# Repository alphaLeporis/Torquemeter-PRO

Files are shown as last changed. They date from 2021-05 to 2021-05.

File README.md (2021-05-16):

# Torquemeter PRO
## Inleiding

Onze koppelmeter is van het type ‘Prony Brake’. Hierbij klemmen we een arm met gekende lengte rond een as zodat de draaibeweging wordt overgebracht op deze arm. Vervolgens meten we op het einde van de arm de kracht die wordt uitgeoefend als gevolg van de draaibeweging.

Omdat de lengte van de arm gekend is kunnen we erg gemakkelijk het koppel bepalen via de volgende formule:

$\tau=L\cdot F$

Deze arm wordt op zijn plaats geklemd door twee bouten die langs weerszijden van de as bevestigd worden. Om de as te beschermen hebben we een bronzen lager tussen de klem en de as. Tijdens het draaien zal deze eerder verslijten dan de klem en de hoofdas. Deze is daarom ook makkelijk vervangbaar.

## Onderdelen

### De load cell

Een load cell bestaat uit een folie met elektrische geleiders. Door vervorming wijzigt de weerstand van deze geleiders. Dit zorgt voor een signaal dat evenredig is aan de kracht die erop wordt uitgeoefend.

Voor onze opstelling gebruikten we een TAL220B 5kg load cell. Deze load cell heeft een spanning nodig van 3V-10V en heeft een meetbereik van 5kg. Deze load cell heeft 4 draden (rood, groen, zwart en wit).  Excitation spanning bepaalt het bereik waarin het uitgangssignaal zit.

### De load cell amplifier

Een load cell amplifier versterkt het signaal van de load cell. Dit is nodig omdat de load cell een zwak signaal geeft (dit komt omdat er anders plastische vervorming zal treden in de load cell).

We gebruiken de hx711 load cell amplifier. Je verbindt de draden van de load cell met de overeenkomstige kleur van de amplifier.

### De lichtsluis

We hebben de RE08A lichtsluis gebruikt. Deze lichtsluis heeft een voedingsspanning nodig 4,5V-5,5V. Met de lichtsluis meten we het aantal keren dat een tand van de schijf er doorheen gaat. Hieruit leiden we het aantal toeren per minuut af die de roterende as van de testbank maakt. Voor deze RPM-sensor hebben we zowel een houder als een schijf ge-3D-print.

## Gebruik

1. Zorg dat de arm en load cell geen contact maken
2. Controleer dat op het LCD-scherm het volgende zichtbaar is (Indien niet: zie “Het op- en afstellen van het project” deel: “**Arduino, LCD & Software”)**
3. Start de meting door de RC-wagen te versnellen.
4. Lees de meetgegevens af op het scherm of op de computer
5. Om het vermogen en de paardenkracht af te lezen: Druk op de zwarte knop onder het LCD-scherm.

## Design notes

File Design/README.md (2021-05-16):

# Torquemeter PRO
 Voor 4-Wetenschappelijk Project hebben we een koppelmeter ontworpen die gebruikt kan worden voor een RC-wagen.

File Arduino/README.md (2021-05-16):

# Programmeren Arduino

1. Download de arduino software van de arduino site
2. Clone al de bestanden hierboven
3. Zet de HX711 bestanden en de koppel bestand in 1 map
4. Open de arduino software met koppel
5. In de arduino software, ga naar bibliotheek gebruiken-> zip bestand -> kies de liquidCristal.zip van hierboven.
6. Duw op "code controleren". In deze stap zouden er geen fouten moeten verschijnen
7. Kies de juiste board en programmer
8. Programmeer!

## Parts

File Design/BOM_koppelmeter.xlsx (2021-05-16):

Bill Of Materials
Onderdeel | Stuks | Prijs | Reden tot aankoop | link | Link 2
LCD-scherm | 1 | €7.00 | LABO Om de gegevens te lezen zonder computer, standalone systeem | https://www.tinytronics.nl/shop/nl/display/lcd/lcd-display-16*2-karakters-met-witte-tekst-en-blauwe-backlight-met-i2c-backpack
Arduino Uno | 1 | €19.50 | Om de sensoren uit te lezen en lokaal te verwerken | https://www.tinytronics.nl/shop/nl/platforms/arduino/arduino-uno-r3-smd
 |  | €7.00 | Alternatief | https://www.tinytronics.nl/shop/nl/arduino/main-boards/uno-r3-compatible-usb-b
Jumper headers | 2 | €2.50 | Verbinding maken tussen al de onderdelen | https://www.tinytronics.nl/shop/nl/kabels/prototype-draden/dupont-jumper-draad-male-female-30cm-10-draden
RPM sensor (lichtsluis) | 1 | €3.00 | Het meten van de rpm om zo HP te bepalen | https://www.tinytronics.nl/shop/nl/sensoren/optisch/lichtsluis-sensor-module-10mm
Spanning- en stroomsensor | 1 | €6.00 | Hierdoor kunnen we de efficientie van het voertuig bepalen | https://www.antratek.be/non-invasive-current-sensor-30a | ENKEL STROOM https://opencircuit.be/Product/ACS724-Stroom-Sensor-Carrier-50A-tot-plus-50A | STROOM SPANNING https://www.tinytronics.nl/shop/nl/sensoren/stroom-spanning/ina226-i2c-dc-stroom-en-spanningsmeter-20a-module
Teflon tape | 1 | €2.00 | Dit zorgt voor een wrijving tussen de as en de arm | https://www.brico.be/nl/badkamer-keuken-wonen/verwarming/verwarmingaccessoires/sanivesk-gas-tape-'unitape'-teflon-12m-x-12mm/5329322
Load cell, load cell amp |  |  | Reeds aangekocht!
Connector voor batterij | 1 | €10.00 | Connectie tussen batterij/esc en spanning- en stroomsensor | https://www.toprc.nl/traxxas-wire-harness-id-series-battery-connection.html | NIET NODIG INDIEN NON-INVASIVE CURRENT SENSOR
Power supply | 1 | €8.00 | Power supply voor de arduino standalone | https://www.tinytronics.nl/shop/nl/voedingen/5v-2a-adapter-met-dc-jack
Bouten
Moeren
totaal echte arduino |  | 58
totaal minder echte arduino |  | 45.5

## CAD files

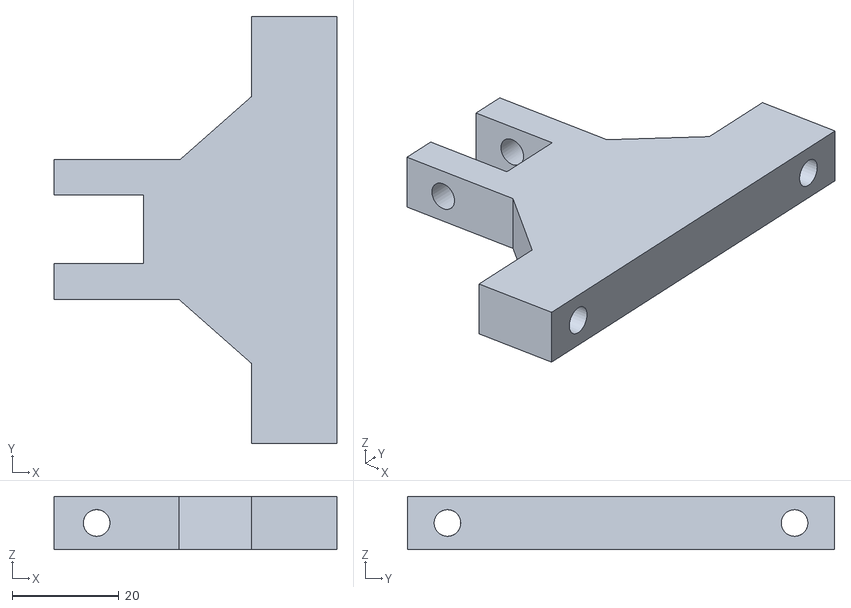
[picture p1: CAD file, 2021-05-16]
Design/Houder Loadcell v4.stl
53.0 x 80.0 x 10.0

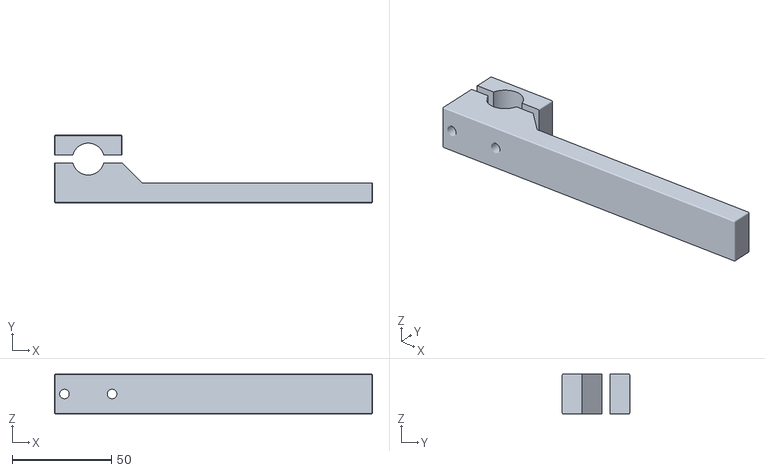
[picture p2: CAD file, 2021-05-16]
Design/arm.stl
160.0 x 34.0 x 20.0

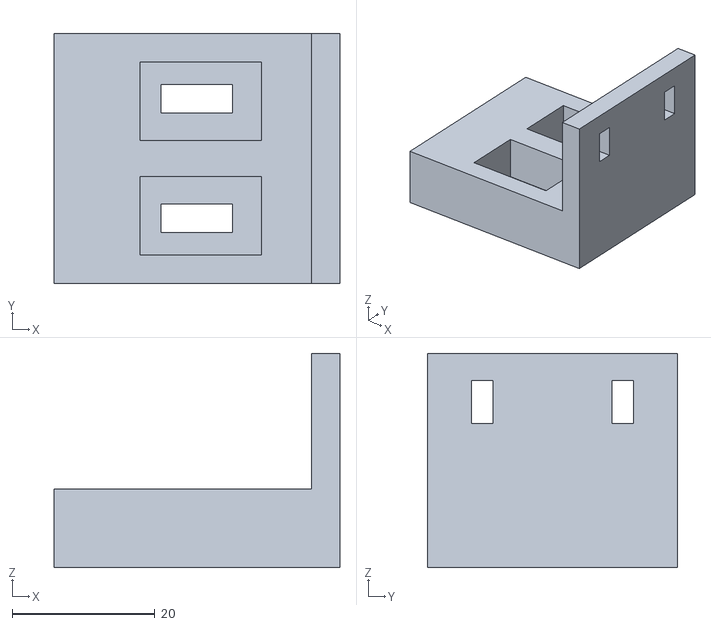
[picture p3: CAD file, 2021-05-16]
Design/rpm_houder.stl
40.0 x 35.0 x 30.0

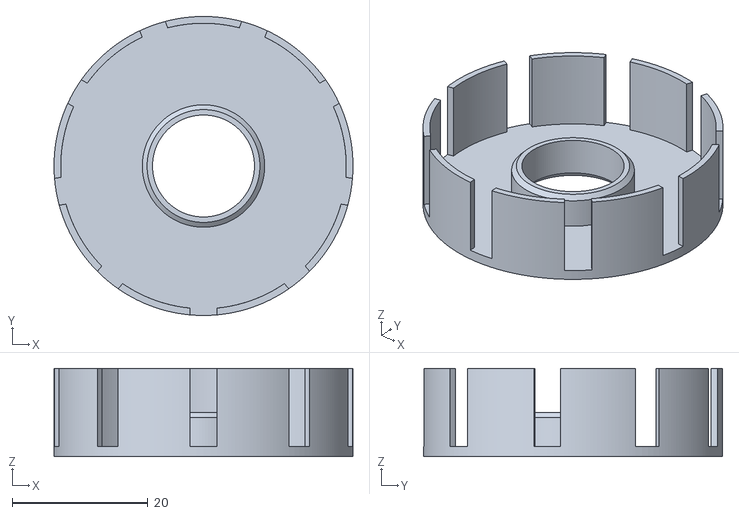
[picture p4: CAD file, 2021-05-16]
Design/rpm_cap_9.stl
44.0 x 44.0 x 13.0

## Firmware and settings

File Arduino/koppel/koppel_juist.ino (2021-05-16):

#include "HX711.h"
#include <Wire.h> 
#include <LiquidCrystal_I2C.h>



//load cell
float calibration_factor = 500; //gevonden via een kalibratie code
#define LOADCELL_DOUT_PIN  5 // verander naar 3 als er problemen zijn
#define LOADCELL_SCK_PIN  4 // verander naar 2 als er problemen zijn
HX711 scale;

int koppel;
float arm = 140; //lengte arm in mm
int vermogen;
int horsepower;
float kracht;



//rpm sensor
const int RPM_pin = 7; //pin op arduino voor RPM sensor
int triggers = 0;
unsigned long elapsedTime;
int laststate =0;
const unsigned long sampleTime = 1000;
int rpmMax=0;
int rpm = 0;


//beeld
LiquidCrystal_I2C lcd(0x3F,16,2);  // set the LCD address to 0x3F for a 16 chars and 2 line display



void setup() {
  Serial.begin(9600);


  //loadcell
  scale.begin(LOADCELL_DOUT_PIN, LOADCELL_SCK_PIN);
  scale.set_scale();
  scale.tare(); //Reset the scale to 0
  long zero_factor = scale.read_average();

  //scherm
  lcd.init(); // initiatie van de scherm
  lcd.backlight();

  //rpm
  pinMode(RPM_pin, INPUT);

  //knop
  pinMode(2, INPUT_PULLUP);  


}

void loop() {

  Koppel();
  Serial.print(";");
  RPM();

  vermogen = (koppel * rpmMax)/9.5488 ;
  //P = T * w
  //w = 2 * pi * n / 60 met n = RPM 
  
  horsepower = vermogen/1341.02;
  
  int knop = digitalRead(2); 
  if (knop == HIGH) { //als knop niet is ingedrukt
  
  //koppel
    lcd.setCursor(0,0); //coördinaat vanaf waar het mag printen
    lcd.print("KOPPEL= ");

    lcd.setCursor(8,0);
    lcd.print(koppel);
    if (koppel < 0) {
      lcd.setCursor(8,0);
      lcd.print("0    ");}
    else if (koppel < 10) {
      lcd.setCursor(9,0);
      lcd.print("  ");
    } else if (koppel < 100) {
      lcd.setCursor(10,0);
      lcd.print("  ");}
    
    lcd.setCursor(13,0);
    lcd.print("Nmm");

    //RPM
    lcd.setCursor(0,1);
    lcd.print("RPM   = ");

    lcd.setCursor(8,1);
    lcd.print(rpmMax);
    if (rpmMax < 10) {
      lcd.setCursor(9,1);
      lcd.print("  ");
    } else if (rpmMax < 100) {
      lcd.setCursor(10,1);
      lcd.print("  ");}
      else if (rpmMax < 1000) {
      lcd.setCursor(11,1);
      lcd.print("  ");
      }

    lcd.setCursor(13,1);
    lcd.print("rpm");  }

    
    else{            //als knop is ingedrukt
      lcd.setCursor(0,0);
      lcd.print("vermogen= ");

    lcd.setCursor(9,0);
    lcd.print(vermogen);
    if (vermogen < 10) {
      lcd.setCursor(10,0);
      lcd.print("  ");
    } else if (vermogen < 100) {
      lcd.setCursor(11,0);
      lcd.print("  ");}

    lcd.setCursor(14,0);
    lcd.print("  ");

    lcd.setCursor(13,0);
    lcd.print("W"); 
  
    lcd.setCursor(0,1);
    lcd.print("horse  = ");

    lcd.setCursor(9,1);
    lcd.print(horsepower);
    if (horsepower < 10) {
      lcd.setCursor(10,1);
      lcd.print("  ");
    } else if (horsepower < 100) {
      lcd.setCursor(11,1);
      lcd.print("  ");}
  
    lcd.setCursor(15,1);
    lcd.print("  ");

    lcd.setCursor(13,1);
    lcd.print("HP");  }

      delay(100); //add a delay

}

void Koppel()
{
  scale.set_scale(calibration_factor); //Adjust to this calibration factor
  
  kracht = ((scale.get_units())/1000 * 9.81);
  koppel = (kracht * arm) ;
  //Serial.print(scale.get_units(), 1); //scale.get_units() returns a float
  //Serial.println(" g");
  Serial.print(koppel);
  //Serial.print(" Nmm;");


  
}


  void RPM() {
  //Serial.print(rpmMax);
  //Serial.println(" RPM");

  Serial.println(rpm);
  rpm=rpmGet();
  //if (rpm > rpmMax)
  //{
    rpmMax = rpm;
  //}
    }

int rpmGet(){
  unsigned long currentTime = 0;
  unsigned long startTime = millis();
  while (currentTime <= sampleTime)
  {
    int val = digitalRead(RPM_pin);
    if(!val)
    {
      if(laststate){
        triggers++;
        laststate=0;
        }
    }
  else {laststate = 1;}
  currentTime = millis() - startTime;
  }

  int countRpm = (triggers*60)/9;
  triggers=0;
  return countRpm;
}
